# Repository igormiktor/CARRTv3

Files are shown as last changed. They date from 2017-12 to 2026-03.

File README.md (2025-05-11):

# CARRTv3
Cute Autonomous Robot Rover Thing (version 3 -- Raspberry Pi Zero 2 W and Raspberry Pico based)

## Goal 

Goal of this project is to create a small robotic vehicle (CARRT) that can do the following:

- Start in one room of the house;
- Receive a goal position, specified relative to its starting location (e.g., 8 meters North, 4.5 meters West);
- Autonomously make its way to the new position, mapping doors and walls with its Lidar sensor until it finds a path to the goal;
- Build a map as it goes, enabling effective back-tracking whenever it encounters a dead-end.

This is both a hardware and a software project.

The name "CARRT" is thanks to my daughter.

## Version 3: What's New?

[Version 2](https://github.com/igormiktor/CARRTv2) was based on an AVR Mega2560 microcontroller, which proved to have too little memory to maintain a suitably accurate and large enough map of its environment (and it was quite slow at calculating paths).  Version 2 was also unable to track its own position and orientation with sufficient accuracy, making usable map updates effectively impossible.

To overcome these problems, Version 3 uses a Raspberry Pi Zero 2 W as its primary processor, paired with a Raspberry Pico to handle real-time tasks.  The Pi Zero has sufficient RAM to maintain a map of its environment with suitable resolution.  Version 3 also has encoders on its wheels and it uses a BNO055 9-DOF sensor with on-board sensor fusion, so that Euler angles and quaternions can be directly read from it.  The combination of wheel-encoders and direct access to orientation information are estimated to provide suffiently accurate orientation and position information. 

## The Hardware and Software

The hardware consists of a four-wheeled chassis carrying a Raspberry Pi Zero 2 W as its primary processor, paired with a Raspberry Pico to handle real-time tasks.  These are complemented by various other supporting IC subsystems (e.g., a motor driver board, a board with an LCD and keypad, a PWM/Servo-driver board, 3V3<->5V level converters, a battery regulator, etc.)  Navigation is enabled by an BNO055 9-DOF orientation sensor and wheel-encoders.  A Garmin Lidar Lite sensor mounted on a servo allows CARRT to sense obstacles (both furniture and walls) and navigate around them.

The hardware and how it is wired together is described in the [`schematics`](https://github.com/igormiktor/CARRTv3/tree/main/schematics) sub-directory by a [KiCad](https://www.kicad.org/) project file, as well as a PDF of the schematics. Photos of CARRT appear in the [`images`](https://github.com/igormiktor/CARRTv3/tree/main/images) sub-directory.

The software is found in the [`source`](https://github.com/igormiktor/CARRTv3/tree/main/source) directory, with subdirectories for the Pi Zero source code ([`source/rpi`](https://github.com/igormiktor/CARRTv3/tree/main/source/rpi)) and the Pico source code ([`source/pico`](https://github.com/igormiktor/CARRTv3/tree/main/source/pico)).  Code common to both is in [`source/shared`](https://github.com/igormiktor/CARRTv3/tree/main/source/shared).   

The Pi Zero uses I2C to control and monitor the motor driver, the LCD & Keypad, the servo, and the Lidar.  The Pico uses real-time interrupts to track the wheel-encoders and uses a separate I2C to control and monitor the BNO055; the Pico also uses an analog input pin to monitor the level of the LiPo battery that powers the IC circuits.  The Pi Zero and the Pico communicate over a serial link connecting their UARTs.

## Power

CARRTv3 is powered from two sources. A LiPo battery connected to a PowerBoost 1000 module provides 5V power to drive all of the IC-related electronics.  The Pi Zero provides a 3V3 power feed for those subcomponents that need 3V3 power.  A six-pack of AA batteries provides 9V power to the four motors that drive the wheels and to the servo that points the Lidar sensor.

## Specs

* Main processor
    * PI Zero 2 W board
    * Broadcom BCM2710A1, quad-core 64-bit SoC (Arm Cortex-A53 @ 1GHz)
    * 512MB LPDDR2
    * 2.4GHz IEEE 802.11b/g/n wireless LAN, Bluetooth 4.2, BLE, onboard antenna
    * 2 x SPI, 1 x I2C, 1 x UART, no ADC
* Secondary microcontroller
    * Pico RP2040 microcontroller
    * Dual-core Arm Cortex M0+ processor, running up to 133 MHz
    * 264KB of SRAM
    * 2MB of on-board flash memory
    * 2 × SPI, 2 × I2C, 2 × UART, 3 × 12-bit ADC
    * Accurate clock and timer on-chip
    * Temperature sensor
* Power buses
    * First power bus supplied by LiPo battery
        * PowerBoost 1000 generates 5V from the LiPo
        * Pi Zero in turn generates 3V3 power for all devices that need it
        * Both 5V and 3V3 available as required (CARRTv3 is primarily a 3V3 system)
    * Second power bus supplied by a six-pack of AA batteries
        * Provides 9V power to the motors 
        * 4 driving motors (one per wheel)
        * 1 servo motor (points the Lidar across a 180 degree arc) 
* Motor controllers
    * Adafruit Raspberry Pi DC & Stepper Motor Bonnet
    * Uses 4 H-Bridges to power 4 DC motors
    * Each H-Bridge is a TB6612 providing 1.2A per bridge
    * Controlled by the Pi Zero via I2C
* LCD display with keypad
    * 2 x 16 character color LCD
    * 5 button keypad
    * LCD controlled by an HD44780U
    * MCP23017 drives the HD44780U and the keypad
    * MCP23017 connected via I2C to Pi Zero
    * Controlled by Pi Zero via I2C
* PowerBoost 1000
    * Converts LiPo battery to 5V
    * Also serves LiPo batter charger (via USB power connection)
    * Provides "power off" control via grounding of an "enable" pin 
    * Battery level pin read by analog Pico pin (level shifted by resistor bridge to 3V3)
* BNO055 9-DOF Orientation Sensor
    * 3 sensors in one device
        * Triaxial 16bit gyroscope
        * Triaxial 14bit accelerometer
        * Geomagnetic sensor
    * 32-bit Cortex M0+ microcontroller runs sensor fusion software,
    * Outputs Euler angles, quaternions, rotation vector, linear acceleration, gravity, heading 
    * Controlled by Pico via I2C
* PCA9685 16-channel PWM/Servo driver
    * 16 independent PWM channels
    * Used to control the servo
    * Controlled by Pi Zero via I2C
    * Servo powered by 9V bus
* TXB0104 Bi-Directional Level Shifter
    * Performs bidirectional level shifting between 5V and 3V3 
    * Auto-detects the direction
    * Not suitable for I2C level-shifting
* BSS138 Bi-Directional Logic Level Shifter
    * 4-channel I2C-safe bidirectional logic level converter 
    * 4 BSS138 FETs with 10K pullups
    * Logic-shift only, no loads possible on high side
* Wheel-encoders 
    * On two front wheels
    * Encoders are 5V subsystems
    * Read by Pico after level-shifting by TXB0104
* Hiwonder HPS-2018MG servo
    * Working voltage 6.8 - 10.4V
    * Rotation range 0 - 180 degress 
    * Servo accuracy 0.3 degrees
    * Pulse period 20ms
    * Duty cycle 0.5ms - 2.5ms
    * Controlled by Pi Zero via I2C via PCA9685
* Garmin Lidar Lite v3
    * Mounted on the HPS-2018MG servo
    * Resolution 1cm
    * Accuracy +/- 2.5cm
    * Range 5cm to 40m
    * Laser wavelength 905nm
    * Lidar is a 5V subsystem
    * Controlled by PI Zero via I2C (level-shifted by BSS138)
* PS1240 piezoelectric buzzer
    * For success beeps and error tones

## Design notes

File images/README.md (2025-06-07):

# The evolution of CARRTv3 

A series of photos capturing the evolution of CARRTv3 from the very beginning of prototyping.

## Prototyping

A very early prototype combined a Raspberry Pi Zero with an Adafruit Pro Trinket (3V3) for realtime tasks. It was powered by 12V from a pack of 8 x AA cells.  This 12V feed powered both all motors and also feed a UBEC to generate 5.2V output to power the ICs.  The prototype also included an LCD with keypad. a 9DOF BNO055 sensor, and a motor-driver board.  The two photos below show the configuration without (left) and with (right) the drive motors connected.  For prototypoing, the various boards and components are velcroed onto a transparent plastic board.

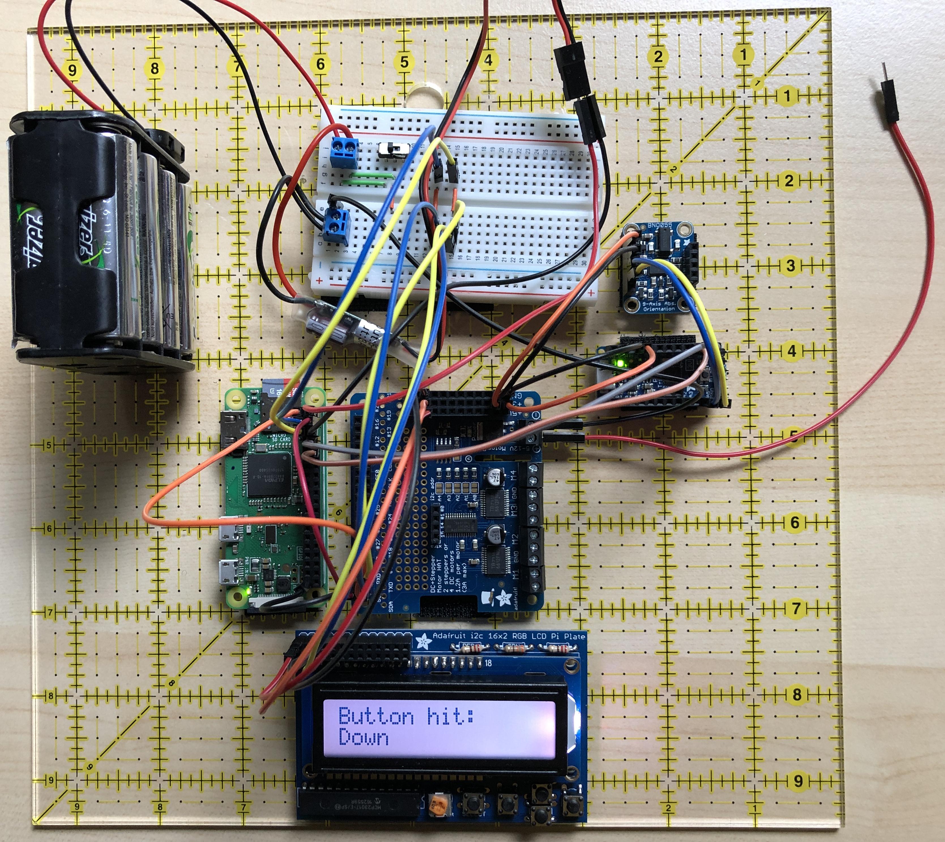
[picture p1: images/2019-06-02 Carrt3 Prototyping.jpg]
Early prototype: RPi Zero, Adafruit Trinket, 9DOF sensor, LCD + keypad, motor board
[]("https://github.com/igormiktor/CARRTv3/blob/main/images/2019-06-02%20Carrt3%20Prototyping.jpg")
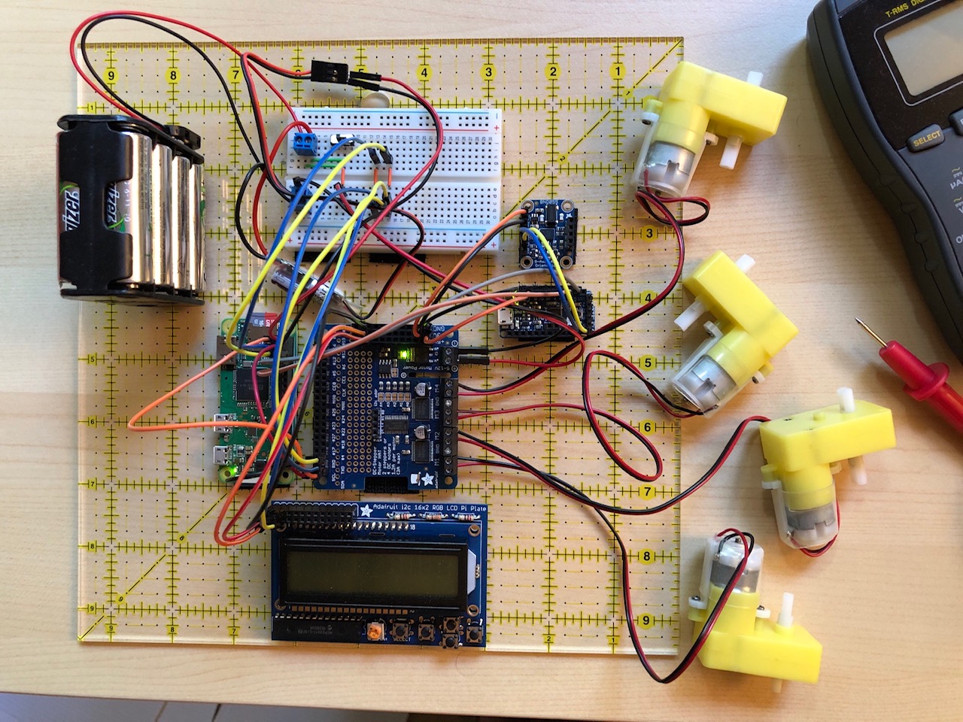
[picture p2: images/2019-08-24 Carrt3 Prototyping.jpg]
Early prototype: RPi Zero, Adafruit Trinket, 9DOF sensor, LCD + keypad, motor board, and motors
[]("https://github.com/igormiktor/CARRTv3/blob/main/images/2019-08-24%20Carrt3%20Prototyping.jpg)

The power source was not sufficently stable to reliably power the RPi Zero (and other ICs).  The boards themselves also took up too much space (cm<sup>2</sup>) to all fit when mounted on the vehicle chassis.  So while useful for initial testing and exploration, the configuration was updated as follows:

* An AdaFruit PowerBoost 1000C, powered by a 3.7v 2,500mAh LiPo battery replaces the 8 x AA cells and UPEC combination to power the RPi Zero (and other ICs).
    * A set of 6 x AA batteries (producing 9V) is retained on a separate power bus to power motors of various kinds.
* An RPi Pico replaces the Adafruit Pro Trinket (3V3).  The Pico provides a much more capable microcontroller, having 2 cores, more memory, and running at 10x the clock speed of the Trinket (133MHz vs 12MHz).
* A much smaller motor board replaces the original motor board.  The original was an RPi "shield" (same footprint as a fullsize RPi). The new one is a much smaller RPI "bonnet", with the much smaller footprint of an RPI Zero.
* A PCA9685 PWM board provides 16 x 12 bit PWM outputs to drive servo motors.

## Organizing Electronics

To facilitate attachment of printed circuit boards (PCBs) and the wiring between these, I created a 3D-printed plastic "riser".  The various PCBs are attached to the riser, allowing wiring to be run under or over the riser, keeping the wiring a bit neater.  The riser (with attached PCBs) is then attached to the chassis.

Not all the PCBs could fit on the riser.  As a result the motor driver PCB (an Adafruit "bonnet") is actually attached underneath the top plate of the chassis (in the area below the breadboards).  A 3D-printed holder for the LiPo battery is also attached underneath the top plate (located roughly under the PowerBoost and the RPi Zero).

Finally, a small breadboard is also installed on the lower plate of the chassis to distribute 9V power to all motors.  That small breadboard also carries an on-off switch for the 9V power circuit and an indicator LED that lights when 9V power is on.  The 9V battery pack (6 x AA) simply sits in the well between the four drive motors.

The following images show (L-to-R):
* The plastic riser with PCBs attached (but not wired).
* The plastic riser adjacent to the assembled chassis.
* The dissassembled (partially wired) chassis showing (L-to-R)
    * The bottom plate, with 4 motors and 9V breadboard.
    * The top plate (inverted), showing the motor driver PCB, and the LiPo battery holder.
    * The riser with PCBs (partially wired for testing).

[Riser Deck, with electronics]("https://github.com/igormiktor/CARRTv3/blob/main/images/2024-05-25%20Electronics%20Deck.jpg")
[Riser deck adjacent to the assembled chassis]("https://github.com/igormiktor/CARRTv3/blob/main/images/2024-05-25%20Chassis%2BElectronics%20Deck.jpg")
[Dissassembled (partially wired) chassis]("https://github.com/igormiktor/CARRTv3/blob/main/images/2024-05-26%20L-to-R%20Chassis%20bottom%2C%20underneath%20Chassis%20top%2C%20Electronics%20deck.jpg")

This layer-cake assembly (and especially the riser carrying the PCBs witht he primary electronics) simplifies assembly and disassembly, and facilitated "test as you assemble.  The following images show how it all comes together (L-to-R):
* The electronics-carrying riser mounted on top of the vehicle chassis.
* The battery-holder mounted under the chassis top plate.
* The battery-holder and motor driver PCB mounted under the chassis top plate.

[Electronics-carrying riser mounted on top of the vehicle chassis]("https://github.com/igormiktor/CARRTv3/blob/main/images/2024-05-25%20Chassis%20with%20Electronics%20Deck.jpg")
[Riser Deck, with electronics]("https://github.com/igormiktor/CARRTv3/blob/main/images/2024-05-25%20Battery%20under%20Chassis%20top.jpg")
[Riser Deck, with electronics]("https://github.com/igormiktor/CARRTv3/blob/main/images/2024-05-25%20Chassis%20%2B%20battery%20holder%20(L)%20%2B%20motor%20driver%20(R).jpg")

## Wiring and Power-up

Wiring and power-up testing started early and continued throughout assembly.  This is depicted in the following images (L-to-R):
* A minimal assembly and wiring under power (electronics on riser only)
* All layers powered, LCD and drive motors running

[Minimal assembly and wiring under power]("https://github.com/igormiktor/CARRTv3/blob/main/images/2024-05-26%20Minimal%20Assembly%20Powered.jpg")
[All layers powered, LCD and drive motors running]("https://github.com/igormiktor/CARRTv3/blob/main/images/2024-06-03%20Motors%20running%20under%20electronic%20control.jpg")

Final wiring was accomplished with hook-up wire (instead of breadboarding wire).  As a general rule, longer wire reaches run under the riser; shorter ones run over the riser and PCBs.  The color code for the hook-up wires is:
| Color  | Purpose |
| :---:  | :--- |
| Black  | Ground |
| Red | Power (5V) |
| Orange | Power (3V3) |
| Blue | I2C SDA (data) |
| Yellow | I2C SCL (clock) |
| Grey | Serial TX-RX |
| Dark Blue | Serial RX-TX |
| Green | PWM and GPIO (various) |
| White | GPIO (various) |

Images below show a nearly fully wired CARRTv3. The only wires missing are those connecting the motor driver PCB and those connecting the Garmin Lidar (which is not yet installed).  These images show views from the front and rear; from the left and right sides; and final a top view.

[Front view]("https://github.com/igormiktor/CARRTv3/blob/main/images/2025-04-08%20CARRTv3%20Front%20View.jpg")
[Rear view]("https://github.com/igormiktor/CARRTv3/blob/main/images/2025-04-08%20CARRTv3%20Rear%20View.jpg")

[Left view]("https://github.com/igormiktor/CARRTv3/blob/main/images/2025-04-08%20CARRTv3%20Left%20View.jpg")
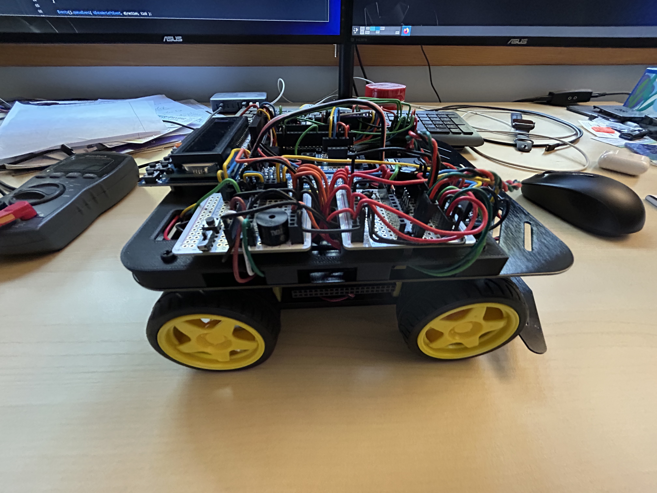
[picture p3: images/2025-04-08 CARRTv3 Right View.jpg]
Right view
[]("https://github.com/igormiktor/CARRTv3/blob/main/images/2025-04-08%20CARRTv3%20Right%20View.jpg")

[Top view]("https://github.com/igormiktor/CARRTv3/blob/main/images/2025-04-08%20CARRTv3%20Top%20View.jpg")

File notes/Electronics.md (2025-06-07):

# Electronics

## Wiring

| Color  | Purpose |
| :---:  | :--- |
| Black  | Ground |
| Red | Power (5 V) |
| Orange | Power (3.3 V) |
| Blue | I2C SDA |
| Yellow | I2C SCL |
| Grey | UART TX-RX |
| Dark Blue | UART RX-TX |
| Green | PWM and GPIO (various) |
| White | GPIO (various) |

## Power Voltages

| Point of Measurement | Voltage |
| :--- | :---: |
| Power Boost 1000C Output (at posts) | 5.19 V |
| RPI Zero Output (at RPi Zero) | 5.14 V |
| On 5V Power Rail | 5.08 V |
| On 3.3V Power Rail | 3.25 V |
| Input to Pico (before diode) | 5.08 V |
| Input to Pico (after diode) | 4.3 V |
| RPI Pico Output (3V) | 3.3 V |
| Motor Batteries Output (at posts) | 10.4 V (8 batteries) |
| Motor Hat (at input) | 10.4 V (8 batteries) |
| Motor Batteries Output (at posts) | 7.8 V (6 batteries) |
| Motor Hat (at input) | 7.8 V (6 batteries) |

## Drive Motor Operations

| Operation | Current |
| :--- | :---: |
| Idle | 0.0007 A |
| Single motor start  | 0.3 - 0.6 A |
| Single motor run | 0.2 - 0.3 A |
| All motor start | 1.2 - 2.5 A |
| All motor run | 0.8 - 0.9 A |

* Switch directly by manual switch on lower (12V) distribution panel

## Raspberry Pi Zero 2 W Operations

| Operation | Current |
| :--- | :---: |
| Idle | 100 mA |
| Start up | 200 mA |
| Computing | 350 mA |

* Switched directly by PowerBoost 1000C using a manual switch (on the upper-rear distribution panel) that grounds the Enable Pin on the PowerBoost.

## Raspberry Pico Operations

| Operation | Current |
| :--- | :---: |
| Idle | 18 mA |
| Start up | 15 mA |
| Max possible  | 200 mA |

* Required switching transistor:  2N2222
* Required transistor base resistor:  2.2 KOhms
* Installed on upper=rear distribution panel
* Automatically switched by RPi Zero via GPIO17 on Pin 11

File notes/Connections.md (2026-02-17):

# Wiring Connections

## Rapsberry Zero

| To | Function | Pin | | Pin | Function | To |
| :---: |  :---: | :---: | :---: | :---: | :---:  | :---: |
| Other 3V3 ICs | 3V3 |  1 |  |  2 | 5V (in) | PowerBoost 5V out |
| I2C Bus RPi0 | I2C SDA |  3 |  |  4 | |  |
| I2C Bus RPi0 | I2C SCL |  5 |  |  6 | | |
| | |  7 |  |  8 | UART TX | Pico UART RX |
| | |  9 |  | 10 | UART RX | Pico UART TX |
| Pico On/Off 2N2222 base  | GPIO17  | 11 |  | 12 |  |  |
| | | 13 |  | 14 | GND | TXB0104 GND |
| | | 15 |  | 16 | GPIO23 | Monitor PowerBoost LPO for battery low |
|  TXB0104 OE Pin | 3V3 | 17 |  | 18 |  |  |
| | | 19 |  | 20 |  |  |
| | | 21 |  | 22 |  |  |
| | | 23 |  | 24 |  |  |
| | | 25 |  | 26 |  |  |
| | | 27 |  | 28 |  |  |
| | | 29 |  | 30 |  |  |
| | | 31 |  | 32 | PWM0 | Buzzer |
| | | 33 |  | 34 | GND | Common Gnd |
| | | 35 |  | 36 | GPIO16 | Shutdown Button |
| | | 37 |  | 38 |  |  |
| | | 39 |  | 40 |  |  |

## Rapsberry Pico

| To | Function | Pin | | Pin | Function | To |
| :---: |  :---: | :---: | :---: | :---: | :---: | :---: |
| Debug RX (Black/Yellow) | UART0 TX |  1 |  | 40 | VBUS | |
| Debug TX (White/Orange) | UART0 RX |  2 |  | 39 | VSYS | 5V Motor Board via 1N4001 diode |
| Debug Gnd (Red/Black) | Gnd |  3 |  | 38 | Gnd | BNO055  |
| | |  4 |  | 37 | | |
| | |  5 |  | 36 | 3V3 | BNO055 |
| RPi0 UART RX | UART1 TX |  6 |  | 35 | | |
| RPi0 UART TX | UART1 RX |  7 |  | 34 | | |
| | |  8 |  | 33 |  |  |
| | |  9 |  | 32 | ADC1 | (GPIO27) ADC to PowerBoost Batt Pin (via V-Divider) |
| | | 10 |  | 31 | ADC0 | (GPIO26) ADC to 9V Batt+ (via V-Divider) |
| I2C Bus Pico | I2C0 SDA | 11 |  | 30 |  |  |
| I2C Bus Pico | I2C0 SCL | 12 |  | 29 |  |  |
| | | 13 |  | 28 |  |  |
| | | 14 |  | 27 |  |  |
| | | 15 |  | 26 |  |  |
| | | 16 |  | 25 |  |  |
| | | 17 |  | 24 |  |  |
| | | 18 |  | 23 | Gnd | Gnd via 2N2222 controlled by Zero GPIO17 |
| Left Encoder | GPIO14 | 19 |  | 22 |  |  |
| Right Encoder | GPIO15 | 20 |  | 21 |  |  |

### Rapsberry Pico SWD (Debug) Pins
(In order from Pin 20 side to Pin 21 side)
| To | Function | Pin |
| :---: |  :---: | :---: |
| Debug CLK (Orange) | SWCLK |  SWD1 | 
| Debug Gnd (Black)  | GND |  SWD2 | 
| Debug IO (Yellow)  | SWIO  |  SWD3 |  

## Adafruit PowerBoost 1000C

| Pin | Function | To |
| :---: | :---: | :---: |
| USB | USB 5V (charge in) |  |
| Bat | Battery Input (3.0-4.2V) | Pico pin 32 (ADC1) via V-Divider |
| Vs | Max(USB, LiPo) |  |
| EN | Enable (Ground to disable) | On/Off Switch |
| GND | Gound |  |
| LBO | Low Battery Signal (toggles from Bat to 0V) | (not 3.3V safe!) RPi0 pin 16 (GPIO23) via TXB0104 |
| GND | Ground | Common Gnd |
| 5Vo | Output 5V (5.2-5.0 V) | Common IC 5V rail  |
|

## BNO055

| Pin | Function | To |
| :---: | :---: | :---: |
| Vin | Power in (3.3-5.0V) | Pico 3V3 |
| 3vo | 3.3V output |  |
| GND | Ground | Pico Gnd |
| SDA | I2C data | Pico I2C0 SDA |
| SCL | I2C clock | Pico I2C0 SCL |
| RST | HW reset (set low, then high) |  |
| PS0 | Mode change pin 0 |  |
| PS1 | Mode change pin 1 |  |
| INT | HW interrupt (goes high 3V) |  |
| ADR | I2C address (default = 0x29; high = 0x28) |  |

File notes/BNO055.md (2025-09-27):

https://learn.adafruit.com/bno055-absolute-orientation-sensor-with-raspberry-pi-and-beaglebone-black/webgl-example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

https://aiinsemi.com/post/Why%20Your%20BNO055%20Sensor%20is%20Giving%20Incorrect%20Data_%20Common%20Calibration%20Issues.html

https://forums.adafruit.com/viewtopic.php?f=25&t=108290&p=541754#p541754

by gammaburst » 16 Dec 2016 22:53
"sensor holds its default configuration P1" -- Do you mean that writing AXIS_REMAP_CONFIG and AXIS_REMAP_SIGN had no effect? Perhaps you are writing them at the wrong time - the Bosch documentation is sometimes vague and insufficient.

Here's my BNO055 startup procedure:
- assert RST
- wait one microsecond
- deassert RST
- wait 800 milliseconds
- (optional) write the two axis remap registers
- (optional) write my previously stored calibration profile into registers 0x55-0x6A
- write 0x0C (NDOF mode) into OPR_MODE register
- wait 10 milliseconds
- begin reading sensor and fusion data registers every 10 milliseconds.

Beware the BNO055 datasheet uses two spellings:
- AXIS_MAP_CONFIG and AXIS_MAP_SIGN
- AXIS_REMAP_CONFIG and AXIS_REMAP_SIGN.

Be sure you have the current BNO055 datasheet version 1.4.

Axises can be remaped only in OPERATION_MODE_CONFIG state.
Reading and writing calibration data is only possible in this state.

How are you testing your quaternion-to-euler conversion? Numbers via the serial port? 3D graphics display? Beware the bunny/Processing example is broken.

Remember to normalize the quaternion.

If you use other people's vector and quaternion equations, beware of different axes conventions. This gets confusing!

During my experiments with Adafruit's BNO055 library I used this code to convert quaternion to Euler. It's one of the fixes that I applied to the bunny/Processing example:

/* Convert quaternion to Euler, because BNO055 Euler data is broken */
  imu::Quaternion q = bno.getQuat();
  q.normalize();
  float temp = q.x();  q.x() = -q.y();  q.y() = temp;
  q.z() = -q.z();
  imu::Vector<3> euler = q.toEuler();
  Serial.print(F("Orientation: "));
  Serial.print(-180/M_PI * euler.x());  // heading, nose-right is positive, z-axis points up
  Serial.print(F(" "));
  Serial.print(-180/M_PI * euler.y());  // roll, rightwing-up is positive, y-axis points forward
  Serial.print(F(" "));
  Serial.print(-180/M_PI * euler.z());  // pitch, nose-down is positive, x-axis points right
  Serial.println(F(""));

I have also successfully used Wikipedia's info and equations:
https://en.wikipedia.org/wiki/Conversio ... Conversion

https://en.wikipedia.org/wiki/Conversion_between_quaternions_and_Euler_angles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

https://forum.arduino.cc/t/convert-adafruit-bno055-quaternion-angles-to-euler-angles/399436/5

float yaw   = atan2(2.0f * (q[1] * q[2] + q[0] * q[3]), q[0] * q[0] + q[1] * q[1] - q[2] * q[2] - q[3] * q[3]);
float pitch = -asin(2.0f * (q[1] * q[3] - q[0] * q[2]));
float roll = atan2(2.0f * (q[0] * q[1] + q[2] * q[3]), q[0] * q[0] - q[1] * q[1] - q[2] * q[2] + q[3] * q[3]);[/quote]

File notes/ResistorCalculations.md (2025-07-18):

# Resistor Calculations

## Motor Battery Level Monitoring

Need to monitor motor battery voltage (nominally 6 x 1.5V = 9V).  
We need to create a resistor divider to ensure the output is not over 3.3V.

### Range of motor battery voltages (6 x AA batteries)
| Type | Full charge | Functionally Dead |
| :---: |  :---: | :---: |
| Akaline | 9.9V | 7.5V |
| NiMH | 8.7V | 7.2V |
| Lithium | 10.8V | 7.8V |

* Input Full V = 8.7 - 10.8 V
* Input Dead V = 7.2 - 7.8 V
* R1 = 180K Ohm
* Output Full V = 2.72 - 3.38 V --> Pico Pin GPIO27
* Output Dead V = 2.35 - 2.44 V --> Pico Pin GPIO27
* R2 = 82K Ohm
* Ground 
* Current through bridge ~0.05 mA  

### Range of measured voltages (at Pico Pin GPIO27)

| Type | Full charge | Functionally Dead |
| :---: |  :---: | :---: |
! Akaline | 3.10V       | 2.35V |
| NiMH    | 2.72V       | 2.25V |
| Lithium | 3.38V       | 2.44V |

## PowerBoost 1000C LBO (Low Battery) Monitoring

LBO drops to 0V when PowerBoost detects battery low voltage (<3.2V).  
However, LBO is pulled up to Vin (up to 5.25V), 
so we need to create a resistor divider to ensure the output 
is always under 3.3V.

* Input V = 5.25 V   <-- PowerBoost LBO Pin
* R1 = 39K Ohm
* Output V = 3.3 V and 0.05 mA  --> Pico Pin GPIO26
* R2 = 68K Ohm
* Ground   

## Encoders

Encoders on the wheels are 5V devices, need to convert them to 3.3V.  
We use the TXB0104 to the the 5V -> 3V3 conversion.

We need two of these conversions (one pair of TXB0104 pins per encoder).

Encoder Pins:

* Pin 1 --> Signal pin (Green)
* Pin 2 <-- +5V power pin (Red)
* Pin 3 --> Gnd (Black)

## Pico power control (on/off from RPi Zero)

Use a 2N2222 transistor on the ground for the Pico to allow the RPi0 to turn it 
on and off

* 2N2222 collector <-- Pico GND
* 2N2222 base <-- 10 KOhm resistor <-- RPi0 GPIO17 (pin 11)
* 2N2222 emitter --> system GND 

Setting RPi0 GPIO17 (pin 11) LOW turns off the Pico; setting RPi0 GPIO17 HIGH turns on the Pico.

## Sources

Resistor calculator: [http://howardtechnical.com/voltage-divider-calculator/](http://howardtechnical.com/voltage-divider-calculator/)

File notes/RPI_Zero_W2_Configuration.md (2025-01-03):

# Raspberry Pi Zero 2 W Configuration

## Goal

Goal is to minize the amperage that the RPi Zero 2 W draws.  Power comes from a LiPo battery through an Adafruit
Powerboost 1000C that has a 2A internal switch (~2.5A peak limiting). The RPi Zero then powers the RP2040 (5V feed) and 
all the secondary chips (3.3V feed).  Motors are powered by a separate power circuit.

## Power Demands

The main power consumers are:

| Device | Recommended Power <br /> Supply Capacity | Typical Bare-Board <br /> Current Draw | Max Board <br /> Current Draw | 
|:---:|:---:|:---:|:---:|
| Raspberry Pi Zero W | 1.2 A | 150 mA | ~0.8 A |
| Raspberry Pi Zero 2 W | 2.0 A | 350 mA | ~1.3 A |
| Raspberry Pico | 0.5 A | 35 mA  | ~100 mA | 

## Minimizing Power Demand

To minimize the RPi Zero power consumption, we make the following configuration changes.

### Turn off blue tooth
To turn off blue tooth (which also makes the best UART available for serial communications) **_add_** the following 
line to `/boot/config.txt` under section `[all]`:

```bash
dtoverlay=disable-bt
```

### Turn off HMDI.
To turn off HMDI first **_comment out_** the following line in `/boot/config.txt`:

```bash
dtoverlay=vc4-kms-v3d
```
and then **_add_** the following line to `/etc/rc.local`:

```bash
/usr/bin/tvservice -o
```

## Provide a Linux shutdown button

To provide a button to trigger a controlled Linux shutdown, I configured GPIO 16 to trigger a controlled
shutdown by adding the following line to `/boot/config.txt` under section `[all]`: 

```bash
dtoverlay=gpio-shutdown,gpio_pin=16,active_low=1,gpio_pull=up
```

And then make sure that in file `/etc/systemd/logind.conf` the line for HandlePowerKey appears as follows:

```bash
HandlePowerKey=poweroff
```

If it is not, the best solution is to create the directory `/etc/systemd/logind.conf.d` and then in that directory
create a file (such as `handlePowerKey.conf` or `poweroff.conf`) containing:

```bash
[Login]
HandlePowerKey=poweroff
```

Note that the default GPIO for poweroff (GPIO 3) is needed for I2C, so it can't be used for the shutdown function.

## Set pigpiod to run

```bash
systemctl enable pigpiod
systemctl start pigpiod
```

## Install wiringpi (especially for the gpio command)

Clone https://github.com/WiringPi/WiringPi and follow the instructions to build and install.

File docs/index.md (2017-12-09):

---
layout: home
#title: CARRT &mdash; an Autonomous Path-Finding Rover
#permalink: /
---

# CARRT v3

Goal of this project is to create a small robotic vehicle (CARRT) that can do the following:

- Start in one room of a house;
- Receive a goal position relative to its current position;
- Autonomously make its way to the goal position, mapping doors and walls with its lidar until it finds a path to the goal;
- Build a map as it goes, enabling effective back-tracking whenever it hits a dead-end.

Version 3 of CARRT is based on a Raspberry Zero W.

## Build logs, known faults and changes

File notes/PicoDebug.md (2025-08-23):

# Connecting RPi Debug Probe to Pico

## Debugger Connections (Debug Port)

Use the orange-black-yellow connector
* Orange wire goes to Pico SWCLK (left Debug pin)
* Black wire goes to Pico GND (middle Debug pin) 
* Yellow wire goes to Pico SWDIO (right Debug pin)

## Serial Connections (UART Port)

Using the white-red-black connector
* White wire goes to Pico Pin 2, GP1
* Red wire goes to Pico Pin 3, GND
* Black wire goes to Pico Pin 1, GP0

Using the orange-black-yellow connector
* Orange wire goes to Pico Pin 2, GP1
* Black wire goes to Pico Pin 3, GND
* Yellow wire goes to Pico Pin 1, GP0

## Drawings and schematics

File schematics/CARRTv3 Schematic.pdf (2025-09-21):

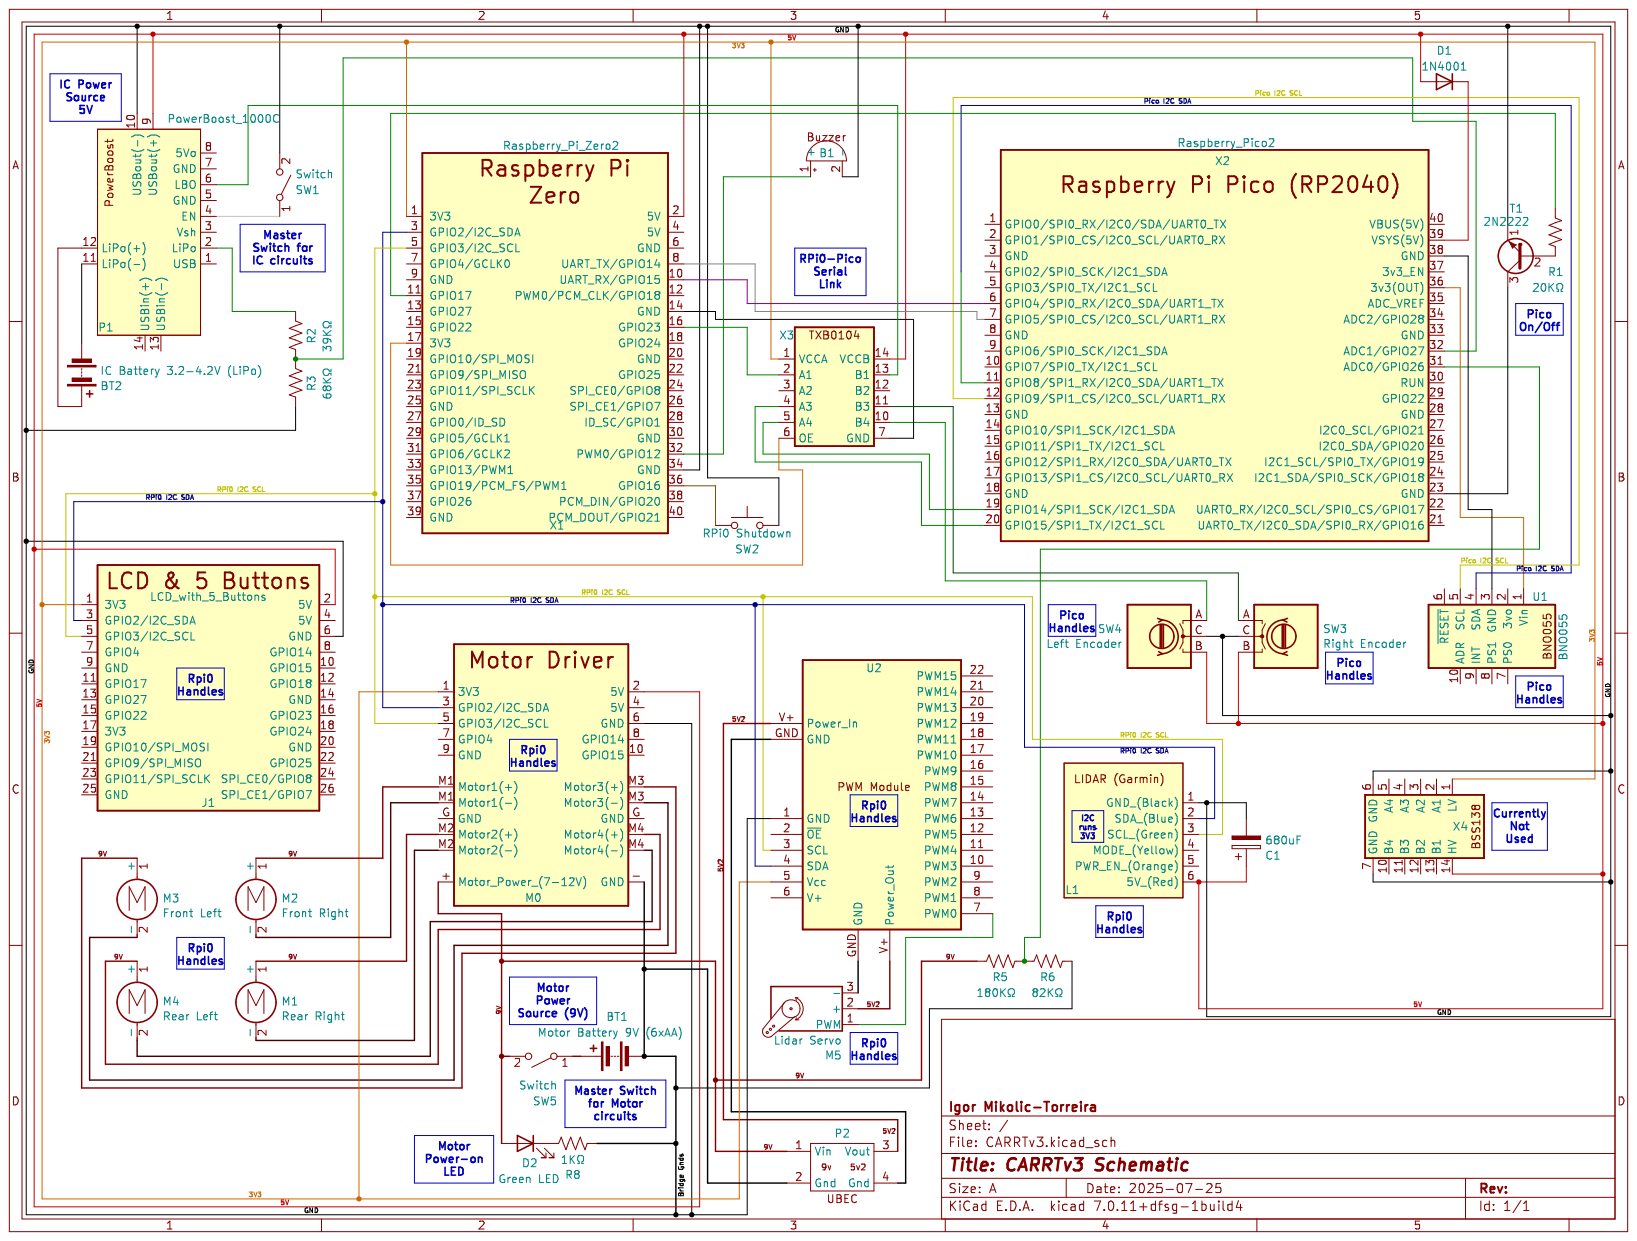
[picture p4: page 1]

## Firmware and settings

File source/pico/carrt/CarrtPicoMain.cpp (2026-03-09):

/*
    CarrtPicoMain.cpp - CARRT-Pico's main function.
    Initializes and hands off to the Main Process.

    Copyright (c) 2026 Igor Mikolic-Torreira.  All right reserved.

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
    You should have received a copy of the GNU General Public License
    along with this program.  If not, see <http://www.gnu.org/licenses/>.
*/

#include "BNO055.h"
#include "Batteries.h"
#include "BuildInfo.h"
#include "CarrtError.h"
#include "CarrtPicoDefines.h"
#include "CarrtPicoReset.h"
#include "Clock.h"
#include "Core1.h"
#include "CoreAtomic.hpp"
#include "DebugUtils.hpp"
#include "Encoders.h"
#include "EventHandlers.h"
#include "EventManager.h"
#include "EventProcessor.h"
#include "HeartBeatLed.h"
#include "I2C.h"
#include "MainProcess.h"
#include "OutputUtils.hpp"
#include "PicoState.h"
#include "SerialLinkPico.h"
#include "SerialMessageProcessor.h"
#include "SerialMessages.h"

#if 0    // Used to test compile definitions inherit properly in cmake build

    #if defined( DEBUGUTILS_ON ) && DEBUGUTILS_ON
        #pragma message "DEBUGUTILS_ON = ON"
    #elif defined( DEBUGUTILS_ON )
        #pragma message "DEBUGUTILS_N = OFF"
    #else
        #pragma message "DEBUGUTILS_N = undef"
    #endif

    #if defined( USE_CARRTPICO_STDIO ) && USE_CARRTPICO_STDIO
        #pragma message "USE_CARRTPICO_STDIO = ON"
    #elif defined( USE_CARRTPICO_STDIO )
        #pragma message "USE_CARRTPICO_STDIO = OFF"
    #else
        #pragma message "USE_CARRTPICO_STDIO = undef"
    #endif

    #if defined( DEBUGCARRTPICO ) && DEBUGCARRTPICO
        #pragma message "DEBUGCARRTPICO = ON"
    #elif defined( DEBUGCARRTPICO )
        #pragma message "DEBUGCARRTPICO = OFF"
    #else
        #pragma message "DEBUGCARRTPICO = undef"
    #endif

    #if defined( BUILDING_FOR_PICO ) && BUILDING_FOR_PICO
        #pragma message "BUILDING_FOR_PICO = ON"
    #elif defined( BUILDING_FOR_PICO )
        #pragma message "BUILDING_FOR_PICO = OFF"
    #else
        #pragma message "BUILDING_FOR_PICO = undef"
    #endif

#endif    // Checking compile definitions

namespace
{
    void initializeNoFailHardware();
    void initializeFailableHardware();
    void setupMessageProcessor( SerialMessageProcessor& smp );
    void setupEventProcessor( EventProcessor& ep );
    void sendReady( SerialLinkPico& link );
}    // namespace

constexpr int kSerialMessageHandlerReserveSize = 24;
constexpr int kEventHandlerReserveSize = 20;

////////////////////////////////////////////////////////////////////////////////

int main()
{
    CoreAtomic::CAtomicInitializer theInitializationIsDone;
    PicoState::initialize();

    initializeNoFailHardware();

    // Open the serial link to RPi0
    SerialLinkPico rpi0;

    try
    {
        initializeFailableHardware();

        output2cout( "CARRT Pico started, hardware initialized, both cores running." );
        output2cout( "CARRT Pico version", CarrtPicoVersion::versionStr(), "with features",
                     CarrtPicoVersion::features() );
        output2cout( "CARRT Pico build date", CarrtPicoVersion::buildDate(),
                     CarrtPicoVersion::buildTime() );
        output2cout( "CARRT Pico Git Hash", CarrtPicoVersion::hashFull() );
        output2cout( "CARRT Pico Git Hash (short)", CarrtPicoVersion::hashShort() );
        if ( CarrtPicoVersion::buildIsDirty() )
        {
            output2cout( "WARNING: CARRT Pico build is DIRTY" );
        }

        // Set up message processor
        SerialMessageProcessor smp( kSerialMessageHandlerReserveSize, rpi0 );
        setupMessageProcessor( smp );

        // Set up event processor
        EventProcessor ep( kEventHandlerReserveSize );
        setupEventProcessor( ep );

        // Report we are started and ready to receive messages
        sendReady( rpi0 );

        // Default starting values
        // (at least for now while testing, RPi0 can change these via msg)
        // TODO: Perhaps eventual make this allMsgsSendOff()
        PicoState::allMsgsSendOn();

        MainProcess::runMainEventLoop( Events(), ep, smp, rpi0 );
    }

    catch ( const CarrtError& e )
    {
        // Expected errors, report the error...
        ErrorReportMsg err( kPicoFatalError, e.errorCode(), Clock::millis() );
        err.sendOut( rpi0 );

        output2cout( "Fatal error", e.errorCode(), e.what() );
    }

    catch ( const std::exception& e )
    {
        // Known but unexpected error, report these...
        int errCode{ makePicoErrorId( kPicoMainError, 1, 0 ) };
        ErrorReportMsg err( kPicoFatalError, errCode, Clock::millis() );
        err.sendOut( rpi0 );

        output2cout( "Fatal error of unexpected nature", e.what() );
    }

    catch ( ... )
    {
        // Unknown errors, report these
        int errCode{ makePicoErrorId( kPicoMainError, 2, 0 ) };
        ErrorReportMsg err( kPicoFatalError, errCode, Clock::millis() );
        err.sendOut( rpi0 );

        output2cout( "Fatal error of unknown type" );
    }

    // From this point, recovering from serious error we can't handle
    // No matter what, this proceess ends in resetting Pico

    output2cout( "Pico frozen and displaying fast LED strobe" );

    // Just spin and put HeartBeatLed on fast strobe
    constexpr int kWaitTimeInMin{ 1 };
    for ( int i{ 0 }; i < kWaitTimeInMin * 60 * 10; ++i )
    {
        Clock::sleep( 100ms );
        HeartBeatLed::toggle();

        // See if we get a sent a reset message
        if ( rpi0.isReadable() )
        {
            auto msgType = rpi0.getMsgType();
            if ( msgType && *msgType == MsgId::kResetPicoMsg )
            {
                PicoReset::reset( rpi0 );
            }
        }

        // If no reset msg, we keep strobing the LED
    }

    // If we get here, just force reset
    output2cout( "Fatal reset" );
    PicoReset::fatalReset();

    return 0;
}

////////////////////////////////////////////////////////////////////////////////

namespace
{

    void initializeNoFailHardware()
    {
        // Nothing in this function throws or even fails

#if USE_CARRTPICO_STDIO
        // Initialize C/C++ stdio (used for status output and debugging)
        stdio_init_all();
#endif

        // Initialize state
        PicoState::initialize();

        // Set up Pico's I2C (to talk with BNO055)
        I2C::initI2C();

        // Initialize the heartbeat LED
        HeartBeatLed::initialize();

        // The encoders are set up on Core1

        // Initialize ADC for batteries
        Batteries::initBatteries();
    }

    void initializeFailableHardware()
    {
        // These function calls may throw

        // Launch Core1
        Core1::launchCore1();

        // If we get here, guaranteed Core1 is running and in its
        // main event loop.  So perfect time to queue this future
        // event to trigger initialization of BNO055.
        // Note future b/c BNO055 needs nearly 1 sec to be ready to accept I2C.
        Core1::queueEventForCore1( EvtId::kBNO055InitializeEvent, BNO055::kWaitAfterPowerOnReset );

        // Tell Core1 to initialize the encoders
        // Core1 does it so the interrupts go to Core1
        Core1::queueEventForCore1( EvtId::kInitEncoders );
    }

    // Debug/test might not call (e.g., use smp in DumpByte mode)
    [[maybe_unused]] void setupMessageProcessor( SerialMessageProcessor& smp )
    {
        // Only register those messages we actually can receive
        // Messages that are only outgoing don't need to be registered
        smp.registerMessage<PingMsg>( MsgId::kPingMsg );
        smp.registerMessage<PingReplyMsg>( MsgId::kPingReplyMsg );
        smp.registerMessage<VersionRequestMsg>( MsgId::kVersionRequestMsg );
        // smp.registerMessage<VersionMsg>( MsgId::kVersionMsg );
        // smp.registerMessage<PicoReadyMsg>( MsgId::kPicoReady );
        // smp.registerMessage<PicoNavStatusUpdateMsg>( MsgId::kPicoNavStatusUpdate );
        // smp.registerMessage<PicoSaysStopMsg>( MsgId::kPicoSaysStop );
        smp.registerMessage<MsgControlMsg>( MsgId::kMsgControlMsg );
        smp.registerMessage<ResetPicoMsg>( MsgId::kResetPicoMsg );
        // smp.registerMessage<TimerEventMsg>( MsgId::kTimerEventMsg );
        smp.registerMessage<TimerControlMsg>( MsgId::kTimerControl );
        smp.registerMessage<BeginCalibrationMsg>( MsgId::kBeginCalibration );
        smp.registerMessage<RequestCalibrationStatusMsg>( MsgId::kRequestCalibStatus );
        // smp.registerMessage<CalibrationInfoUpdateMsg>( MsgId::kCalibrationInfoUpdate );
        smp.registerMessage<SetAutoCalibrateMsg>( MsgId::kSetAutoCalibrate );
        smp.registerMessage<ResetBNO055Msg>( MsgId::kResetBNO055 );
        // smp.registerMessage<NavUpdateMsg>( MsgId::kTimerNavUpdate );
        smp.registerMessage<NavUpdateControlMsg>( MsgId::kNavUpdateControl );
        smp.registerMessage<DrivingStatusUpdateMsg>( MsgId::kDrivingStatusUpdate );
        // smp.registerMessage<EncoderUpdateMsg>( MsgId::kEncoderUpdate );
        smp.registerMessage<EncoderUpdateControlMsg>( MsgId::kEncoderUpdateControl );
        smp.registerMessage<BatteryLevelRequestMsg>( MsgId::kBatteryLevelRequest );
        // smp.registerMessage<BatteryLevelUpdateMsg>( MsgId::kBatteryLevelUpdate );
        // smp.registerMessage<ErrorReportMsg>( MsgId::kErrorReportFromPico );
        smp.registerMessage<TestPicoErrorRptMsg>( MsgId::kTestPicoReportError );
        smp.registerMessage<TestPicoMessagesMsg>( MsgId::kTestPicoMessages );
        // smp.registerMessage<PicoReceivedTestMsg>( MsgId::kPicoReceivedTestMsg );
        smp.registerMessage<DebugLinkMsg>( MsgId::kDebugSerialLink );
    }

    void setupEventProcessor( EventProcessor& ep )
    {
        ep.registerHandler<NullEventHandler>( EvtId::kNullEvent );

        ep.registerHandler<QuarterSecondTimerHandler>( EvtId::kQuarterSecondTimerEvent );
        ep.registerHandler<OneSecondTimerHandler>( EvtId::kOneSecondTimerEvent );
        ep.registerHandler<EightSecondTimerHandler>( EvtId::kEightSecondTimerEvent );

        ep.registerHandler<NavUpdateHandler>( EvtId::kNavUpdateEvent );
        ep.registerHandler<InitializeBNO055Handler>( EvtId::kBNO055InitializeEvent );
        ep.registerHandler<BNO055ResetHandler>( EvtId::kBNO055ResetEvent );
        ep.registerHandler<BeginCalibrationHandler>( EvtId::kBNO055BeginCalibrationEvent );
        ep.registerHandler<SendCalibrationInfoHandler>( EvtId::kSendCalibrationInfoEvent );

        ep.registerHandler<PulsePicoLedHandler>( EvtId::kPulsePicoLedEvent );

        ep.registerHandler<PicoResetHandler>( EvtId::kPicoResetEvent );

        ep.registerHandler<ErrorEventHandler>( EvtId::kErrorEvent );
    }

    void sendReady( SerialLinkPico& link )
    {
        std::uint32_t timeTick{ Clock::millis() };
        PicoReadyMsg ready( timeTick );
        ready.sendOut( link );

        output2cout( "CARRT Pico is ready" );
    }

}    // namespace

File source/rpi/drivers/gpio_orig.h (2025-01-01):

#ifndef PIGPIO_H
#define PIGPIO_H

#include <stddef.h>
#include <stdint.h>
#include <pthread.h>

#define PIGPIO_VERSION 79



#define PI_INPFIFO "/dev/pigpio"
#define PI_OUTFIFO "/dev/pigout"
#define PI_ERRFIFO "/dev/pigerr"

#define PI_ENVPORT "PIGPIO_PORT"
#define PI_ENVADDR "PIGPIO_ADDR"

#define PI_LOCKFILE "/var/run/pigpio.pid"

#define PI_I2C_COMBINED "/sys/module/i2c_bcm2708/parameters/combined"

#ifdef __cplusplus
extern "C" {
#endif

typedef struct
{
   uint16_t func;
   uint16_t size;
} gpioHeader_t;

typedef struct
{
   size_t size;
   void *ptr;
   uint32_t data;
} gpioExtent_t;

typedef struct
{
   uint32_t tick;
   uint32_t level;
} gpioSample_t;

typedef struct
{
   uint16_t seqno;
   uint16_t flags;
   uint32_t tick;
   uint32_t level;
} gpioReport_t;

typedef struct
{
   uint32_t gpioOn;
   uint32_t gpioOff;
   uint32_t usDelay;
} gpioPulse_t;

#define WAVE_FLAG_READ  1
#define WAVE_FLAG_TICK  2

typedef struct
{
   uint32_t gpioOn;
   uint32_t gpioOff;
   uint32_t usDelay;
   uint32_t flags;
} rawWave_t;


typedef struct
{
   uint16_t botCB;
   uint16_t topCB;
   uint16_t botOOL;
   uint16_t topOOL;
   uint16_t deleted;
   uint16_t numCB;
   uint16_t numBOOL;
   uint16_t numTOOL;
} rawWaveInfo_t;

typedef struct
{
   int clk;
   int mosi;
   int miso;
   int ss_pol;
   int ss_us;
   int clk_pol;
   int clk_pha;
   int clk_us;
} rawSPI_t;

typedef struct {
   uint32_t info;
   uint32_t src;
   uint32_t dst;
   uint32_t length;
   uint32_t stride;
   uint32_t next;
   uint32_t pad[2];
} rawCbs_t;

typedef struct
{
   uint16_t addr;
   uint16_t flags;
   uint16_t len;
   uint8_t  *buf;
} pi_i2c_msg_t;


#define BSC_FIFO_SIZE 512

typedef struct
{
   uint32_t control;
   int rxCnt;
   char rxBuf[BSC_FIFO_SIZE];
   int txCnt;
   char txBuf[BSC_FIFO_SIZE];
} bsc_xfer_t;


typedef void (*gpioAlertFunc_t)    (int      gpio,
                                    int      level,
                                    uint32_t tick);

typedef void (*gpioAlertFuncEx_t)  (int      gpio,
                                    int      level,
                                    uint32_t tick,
                                    void    *userdata);

typedef void (*eventFunc_t)        (int      event,
                                    uint32_t tick);

typedef void (*eventFuncEx_t)      (int      event,
                                    uint32_t tick,
                                    void    *userdata);

typedef void (*gpioISRFunc_t)      (int      gpio,
                                    int      level,
                                    uint32_t tick);

typedef void (*gpioISRFuncEx_t)    (int      gpio,
                                    int      level,
                                    uint32_t tick,
                                    void    *userdata);

typedef void (*gpioTimerFunc_t)    (void);

typedef void (*gpioTimerFuncEx_t)  (void *userdata);

typedef void (*gpioSignalFunc_t)   (int signum);

typedef void (*gpioSignalFuncEx_t) (int    signum,
                                    void  *userdata);

typedef void (*gpioGetSamplesFunc_t)   (const gpioSample_t *samples,
                                        int                 numSamples);

typedef void (*gpioGetSamplesFuncEx_t) (const gpioSample_t *samples,
                                        int                 numSamples,
                                        void               *userdata);

typedef void *(gpioThreadFunc_t) (void *);



#define PI_MIN_GPIO       0
#define PI_MAX_GPIO      53


#define PI_MAX_USER_GPIO 31


#define PI_OFF   0
#define PI_ON    1

#define PI_CLEAR 0
#define PI_SET   1

#define PI_LOW   0
#define PI_HIGH  1


#define PI_TIMEOUT 2


#define PI_INPUT  0
#define PI_OUTPUT 1
#define PI_ALT0   4
#define PI_ALT1   5
#define PI_ALT2   6
#define PI_ALT3   7
#define PI_ALT4   3
#define PI_ALT5   2


#define PI_PUD_OFF  0
#define PI_PUD_DOWN 1
#define PI_PUD_UP   2


#define PI_DEFAULT_DUTYCYCLE_RANGE   255


#define PI_MIN_DUTYCYCLE_RANGE        25
#define PI_MAX_DUTYCYCLE_RANGE     40000


#define PI_SERVO_OFF 0
#define PI_MIN_SERVO_PULSEWIDTH 500
#define PI_MAX_SERVO_PULSEWIDTH 2500


#define PI_HW_PWM_MIN_FREQ 1
#define PI_HW_PWM_MAX_FREQ      125000000
#define PI_HW_PWM_MAX_FREQ_2711 187500000
#define PI_HW_PWM_RANGE 1000000


#define PI_HW_CLK_MIN_FREQ       4689
#define PI_HW_CLK_MIN_FREQ_2711 13184
#define PI_HW_CLK_MAX_FREQ      250000000
#define PI_HW_CLK_MAX_FREQ_2711 375000000

#define PI_NOTIFY_SLOTS  32

#define PI_NTFY_FLAGS_EVENT    (1 <<7)
#define PI_NTFY_FLAGS_ALIVE    (1 <<6)
#define PI_NTFY_FLAGS_WDOG     (1 <<5)
#define PI_NTFY_FLAGS_BIT(x) (((x)<<0)&31)

#define PI_WAVE_BLOCKS     4
#define PI_WAVE_MAX_PULSES (PI_WAVE_BLOCKS * 3000)
#define PI_WAVE_MAX_CHARS  (PI_WAVE_BLOCKS *  300)

#define PI_BB_I2C_MIN_BAUD     50
#define PI_BB_I2C_MAX_BAUD 500000

#define PI_BB_SPI_MIN_BAUD     50
#define PI_BB_SPI_MAX_BAUD 250000

#define PI_BB_SER_MIN_BAUD     50
#define PI_BB_SER_MAX_BAUD 250000
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

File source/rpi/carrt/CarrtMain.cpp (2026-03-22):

#include <iostream>

#include "CarrtPigpio.h"
#include "DebugUtils.hpp"
#include "OutputUtils.hpp"



#if 0   // Use this to test that compile definitions inherit properly in cmake build

#if defined( USE_CARRTRPI0_STDIO ) && DEBUGUTILS_ON
    #pragma message "DEBUGUTILS_ON = ON"
#elif defined( USE_CARRTRPI0_STDIO )
    #pragma message "DEBUGUTILS_ON = OFF"
#else
    #pragma message "DEBUGUTILS_ON = undef"
#endif

#if defined( USE_CARRTRPI0_STDIO ) && USE_CARRTRPI0_STDIO
    #pragma message "USE_CARRTRPI0_STDIO = ON"
#elif defined( USE_CARRTRPI0_STDIO )
    #pragma message "USE_CARRTRPI0_STDIO = OFF"
#else
    #pragma message "USE_CARRTRPI0_STDIO = undef"
#endif

#if defined( DEBUGRPI0 ) && DEBUGRPI0
    #pragma message "DEBUGRPI0 = ON"
#elif defined( DEBUGRPI0 ) 
    #pragma message "DEBUGRPI0 = OFF"
#else
    #pragma message "DEBUGRPI0 = undef"
#endif

#if defined( BUILDING_FOR_RPI0 ) && BUILDING_FOR_RPI0
    #pragma message "BUILDING_FOR_RPI0 = ON"
#elif defined( BUILDING_FOR_RPI0 ) 
    #pragma message "BUILDING_FOR_RPI0 = OFF"
#else
    #pragma message "BUILDING_FOR_RPI0 = undef"
#endif

#if defined( USE_PIGPIOD ) && USE_PIGPIOD
    #pragma message "USE_PIGPIOD = ON"
#elif defined( USE_PIGPIOD ) 
    #pragma message "USE_PIGPIOD = OFF"
#else
    #pragma message "USE_PIGPIOD = undef"
#endif

#endif  // Checking compile definitions



int main(int, char**)
{
    gpioInitialise();

    std::cout << "Hello, from CarrtRpi!\n";

    debugM( "This is a debug message" );

    output2cout( "This is a conditional stdio message" );

    gpioTerminate();
}

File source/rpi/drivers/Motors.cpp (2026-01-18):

/*
    Motors.cpp - Functions for controlling CARRTv3's drive motors

    Copyright (c) 2026 Igor Mikolic-Torreira.  All right reserved.

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
    You should have received a copy of the GNU General Public License
    along with this program.  If not, see <http://www.gnu.org/licenses/>.
*/

#include "Motors.h"

#include <cstdint>

#include "I2c.h"
#include "PCA9685.h"

// Extend namespace with additional functions and such
namespace Motors
{

    enum
    {
        kRightRearMotorNbr = 0,
        kRightFrontMotorNbr = 1,
        kLeftFrontMotorNbr = 2,
        kLeftRearMotorNbr = 3
    };

    const int kNbrMotors = 4;

    const std::uint8_t kMotorHatAddress = 0x60;

    class Motor
    {
    public:
        Motor( int pwmPin, int pinA, int pinB );
        ~Motor();

        void goForward() { motorCommand( Motors::kCmdForward ); }

        void goBackward() { motorCommand( Motors::kCmdBackward ); }

        void stop() { motorCommand( Motors::kCmdRelease ); }

        void motorCommand( Motors::MotorCmd cmd );
        void setSpeed( int speed );

    private:
        std::uint8_t mPwmPin;
        std::uint8_t mPinA;
        std::uint8_t mPinB;
    };

    void motorCommand( std::uint8_t motorA, std::uint8_t motorB,
                       std::uint8_t cmd );

    Motor* mMotors[ kNbrMotors ];

};    // namespace Motors

Motors::Motor::Motor( int pwmPin, int pinA, int pinB )
    : mPwmPin( static_cast<std::uint8_t>( pwmPin ) ),
      mPinA( static_cast<std::uint8_t>( pinA ) ),
      mPinB( static_cast<std::uint8_t>( pinB ) )
{
    // Nothing else to do
}

Motors::Motor::~Motor() { stop(); }

[[maybe_unused]]
void Motors::Motor::motorCommand( Motors::MotorCmd cmd )
{
    switch ( cmd )
    {
        case Motors::kCmdForward:
            // Set pin A = 1;
            // Set pin B = 0;
            PCA9685::setOn( kMotorHatAddress, mPinA );
            PCA9685::setOff( kMotorHatAddress, mPinB );
            break;

        case Motors::kCmdBackward:
            // Set pinA = 0;
            // Set pinB = 1;
            PCA9685::setOff( kMotorHatAddress, mPinA );
            PCA9685::setOn( kMotorHatAddress, mPinB );
            break;

        case Motors::kCmdRelease:
        case Motors::kCmdBrake:
            // Set PinA = 0;
            // Set PinB = 0;
            PCA9685::setOff( kMotorHatAddress, mPinA );
            PCA9685::setOff( kMotorHatAddress, mPinB );
            break;
    }
}

void Motors::Motor::setSpeed( int speed )
{
    PCA9685::setPwm( kMotorHatAddress, mPwmPin, 0,
                     static_cast<std::uint16_t>( speed * 16 ) );
}

void Motors::init()
{
    PCA9685::init( kMotorHatAddress );

    mMotors[ 0 ] = new Motor( 8, 9, 10 );
    mMotors[ 1 ] = new Motor( 13, 12, 11 );
    mMotors[ 2 ] = new Motor( 2, 3, 4 );
    mMotors[ 3 ] = new Motor( 7, 6, 5 );

    setSpeedAllMotors( Motors::kFullSpeed );
}

void Motors::setSpeedAllMotors( int speed )
{
    for ( int i = 0; i < kNbrMotors; ++i )
    {
        mMotors[ i ]->setSpeed( speed );
    }
}

void Motors::goForward()
{
    for ( int i = 0; i < kNbrMotors; ++i )
    {
        mMotors[ i ]->goForward();
    }
}

void Motors::goBackward()
{
    for ( int i = 0; i < kNbrMotors; ++i )
    {
        mMotors[ i ]->goBackward();
    }
}

void Motors::stop()
{
    for ( int i = 0; i < kNbrMotors; ++i )
    {
        mMotors[ i ]->stop();
    }
}

void Motors::rotateLeft()
{
    // Right side goes forward
    mMotors[ Motors::kRightFrontMotorNbr ]->goForward();
    mMotors[ Motors::kRightRearMotorNbr ]->goForward();

    // Left side goes backward
    mMotors[ Motors::kLeftFrontMotorNbr ]->goBackward();
    mMotors[ Motors::kLeftRearMotorNbr ]->goBackward();
}

void Motors::rotateRight()
{
    // Right side goes backward
    mMotors[ Motors::kRightFrontMotorNbr ]->goBackward();
    mMotors[ Motors::kRightRearMotorNbr ]->goBackward();

    // Left side goes forward
    mMotors[ Motors::kLeftFrontMotorNbr ]->goForward();
    mMotors[ Motors::kLeftRearMotorNbr ]->goForward();
}

[[maybe_unused]]
void Motors::setRearRightMotorSpeed( int s )
{
    mMotors[ Motors::kRightRearMotorNbr ]->setSpeed( s );
}

[[maybe_unused]]
void Motors::setFrontRightMotorSpeed( int s )
{
    mMotors[ Motors::kRightFrontMotorNbr ]->setSpeed( s );
}

[[maybe_unused]]
void Motors::setFrontLeftMotorSpeed( int s )
{
    mMotors[ Motors::kLeftFrontMotorNbr ]->setSpeed( s );
}

[[maybe_unused]]
void Motors::setRearLeftMotorSpeed( int s )
{
    mMotors[ Motors::kLeftRearMotorNbr ]->setSpeed( s );
}

[[maybe_unused]]
void Motors::runRearRightMotor( Motors::MotorCmd cmd )
{
    mMotors[ Motors::kRightRearMotorNbr ]->motorCommand( cmd );
}

[[maybe_unused]]
void Motors::runFrontRightMotor( Motors::MotorCmd cmd )
{
    mMotors[ Motors::kRightFrontMotorNbr ]->motorCommand( cmd );
}

[[maybe_unused]]
void Motors::runFrontLeftMotor( Motors::MotorCmd cmd )
{
    mMotors[ Motors::kLeftFrontMotorNbr ]->motorCommand( cmd );
}

[[maybe_unused]]
void Motors::runRearLeftMotor( Motors::MotorCmd cmd )
{
    mMotors[ Motors::kLeftRearMotorNbr ]->motorCommand( cmd );
}

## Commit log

2017-11-11 Initial versions of most fundamental drivers
2017-11-11 Standardized the error reporting in the i2c driver
    [I2c.cpp]
2017-11-12 Correct return values to be -1 for error, 0 for no error
    [I2c.cpp]
2017-11-12 Add print() functions to the LCD capabilities (using templates)
2017-11-12 Implement millis() and micros() functions
2017-11-12 Cut down the number of test loops
2017-11-19 Restore error reporting via cerr
    [I2c.cpp]
2017-11-19 Add driver for PCA9685 PWM board
2017-11-19 Correct compiler errors for PCA9685 driver
    [PCA9685.cpp]
2017-11-19 Correct typo in function name
    [PCA9685.cpp]
2017-11-30 Add a setPin() function to PCA9685 driver
2017-11-30 Initial commit of motor drivers
2017-11-30 Complete funtion implementation and fix up return types
    [Motors.cpp]
2019-06-02 Shift error handling to be exception-based
    [I2c.cpp, Lcd.cpp, PCA9685.cpp]
2019-06-02 Add photo of CARRT3 prototype for testing electronics
2019-06-05 Add try-catch blocks to test drivers.
2019-06-09 Added Driver code (and tests) for the motors that power the wheels
2019-06-09 Minor tweaks to test drivers for keypad and lcd
2019-06-09 Adjust timings on collective motor test to allow current measurements
2019-06-09 Update with transistor and resistor calculation results
2019-06-10 Convert i2c to use pigpio library
2019-06-11 Fix with correct pigpio function call for i2c block data transfer
    [I2c.cpp]
2019-06-11 Implement error code scheme that uniquely identifies modules and functions
    [I2c.cpp]
2019-08-24 Photo showing prototype board with motors connected (and working)
2023-11-19 Initial checkin, switch from AVR to PICO
2023-11-23 Fixes (primary: us to ms; big oops!)
    [CarrtPicoMain.cpp]
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2023-12-02 Be more careful with I2C in KeypadTest
2023-12-03 Update with poweroff button config info
2023-12-08 Update to use new error ID creation function
    [I2c.cpp]
2023-12-10 Update info for 6 battery motor configuration
2023-12-10 Update wiring color scheme
2023-12-10 Add PowerBoost and BNO055 connections
2024-06-08 Fix I2C error throws
    [I2c.cpp]
2024-06-09 Add notes on wiring Pico debugger
2024-06-19 Add binary info to pico builds
2024-06-23 Start fleshing out cmds between Pi-0 and Pico
2024-06-27 Make a shared error code scheme
    [I2c.cpp]
2024-06-28 Test exception handling in Pico build
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2024-07-06 Add a check on how long the interrupt takes
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2024-07-06 Fix names of #defines to avoid clashes with SDK
    [CarrtPicoBinaryInfo.cpp, CarrtPicoDefines.h, CarrtPicoMain.cpp]
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2024-07-07 Use heartbeat LED to signal trouble with a fast pulse
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2024-07-08 Test Pico reset/reboot.
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2024-07-23 Added function to submodule to get all calibration statuses at once
2024-07-25 Revise start-up process because of the way BNO055 calibration works
2024-07-26 Mark that we need to fix error handling here
    [Core1.cpp]
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2024-12-27 Add schematics
    [CARRTv3.kicad_pcb, CARRTv3.kicad_sch]
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2024-12-27 Added level-shifters, LIDAR, etc
    [CARRTv3.kicad_sch]
2024-12-28 Updated to use voltage shifters
    [CARRTv3.kicad_sch]
2024-12-28 Update gitignore to omit PDFs except the schematic PDF
2024-12-28 Color-coded the wiring
    [CARRTv3.kicad_sch]
2024-12-29 Cleaned up wiring, added labels
    [CARRTv3.kicad_sch]
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2024-12-31 Add buzzer, missing OE & GND wires, clean up wiring
    [CARRTv3.kicad_sch]
2025-01-01 add cmake infrastructure for switching pigpio <-> pigpiod
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2025-01-04 Fix erroneous type cast
    [I2c.cpp]
2025-01-04 Update to exact pins being used; update colors of wires to actual; cosmetic repositionings
    [CARRTv3.kicad_sch]
2025-03-02 Updated schematics to reflect implementation wiring adjustments
    [CARRTv3.kicad_sch]
2025-04-06 Correct current values
2025-04-06 Reflect actual wiring of BSS138
    [CARRTv3.kicad_sch]
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2025-04-09 Initial fully wired assembly (missing Lidar)
2025-07-02 Make RPi0 pin assignments explicit in one header
2025-07-02 Add buzzer driver and test
    [Buzzer.cpp]
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2025-07-20 Initial checkin of Lidar code from old-carrt (needs conversion)
2025-07-22 Initial conversion of Lidar (with some new I2C functions too)
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2025-07-25 Update schematics for UBEC, etc
    [CARRTv3.kicad_sch]
2025-07-26 Switch ADC0-ADC1 connections; update schematic and connections tables
    [CARRTv3.kicad_sch]
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2025-08-03 Create Serial link implementation for Pico (and fix little serial things in the process)
    [I2C.cpp, SerialLinkPico.cpp]
2025-08-04 Back to block reading over uart. Now working.
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2025-08-09 Switch to using references, not pointers in CriticalSection
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2025-08-23 Update connections notes to include Pico SWD connects
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2025-08-30 Fix typo in Encoders.cpp
    [Encoders.cpp]
2025-08-30 Fix error in 1/4s events, clean up code a bit
    [Core1.cpp]
2025-08-30 Small fixes to BNO055 code and CMakeLists.txt files
    [BNO055.cpp]
2025-08-30 Manage state info in Pico with singleton (can accomodate atomic if needed)
2025-08-31 Added more cmds, including reset (pico) and implementation for this. Ordered commands in code by orderof Cmd IDs in SerialCommand.h
    [CarrtPicoMain.cpp]
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2025-09-05 Make I2C functions used by BNO055.c library code extern "C"
2025-09-21 Correct I2C connects at Pico
    [CARRTv3.kicad_sch]
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2025-09-27 Fix I2C implementation for comms with BNO055
    [I2C.cpp]
2025-10-06 Fix loading of calib status struct
    [BNO055.cpp]
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2025-10-06 Implement calibration cmds and fix some bugs
2025-10-11 Clean up events and code related to nav calibration
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2025-10-11 Add BNO reset event
    [Core1.cpp]
2025-10-11 Improve BNO055 init and reset to avoid event queue overflows
    [BNO055.cpp]
2025-10-12 Incorporate lessons from BNOTest into Carrt Pico itself
2025-10-13 Set reserve size for classes with unordered_maps; fix missing includes
    [CarrtPicoMain.cpp]
2025-10-13 Add msg to control msg sending from Pico
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2025-10-20 Implement message to test error reporting. Also make sure never dual "takeAction()"
    [CarrtPicoMain.cpp]
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2025-10-26 Fix handling of calibration begin and add new autoCalibration mode/state.
    [Core1.cpp]
2025-10-27 Track whether we are in startup mode (some calibration reporting and calibration itself needs to be off during startup)
2025-10-29 Configyre encoders to interrupt on Core1 (not Core0)
2025-11-02 Made OutputUtils adapted to both RPi0 and Pico
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2025-11-15 Switch to target_sources in CMakeLists and also omit compile defs and options inherited from libs in cmake build
2025-11-15 Add optional code to check correct inherit of compile opts and defs
    [CarrtMain.cpp]
2025-11-15 Improve code for checking compile opts/defs inherited from libs correctly
    [CarrtPicoMain.cpp]
2025-11-18 Add ability to control individual timer events (not all or nothing)
2025-11-18 Ensure path for "pico.h" in included in config (needed to include "OutputUtils.h")
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2025-11-27 This is the serial FIX (Pico needs small pause for serial traffic to arrive in sequential element reads)
2025-11-27 Roll-back debugging code (problem fixed)
    [CarrtPicoMain.cpp]
2025-11-27 Rename ResetMsg to ResetPicoMsg for clarity
    [CarrtPicoMain.cpp]
2025-11-27 Pico also sends ResetPicoMsg (to inform RPi it is resetting
2025-11-28 Refine Pico delays (and min delay for sequential serial reads)
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2025-11-28 Update how timer and nav msgs are turned on/off via msgs from RPi)=0
2025-12-28 For testing, add ack of msg requested by RPi0 but that Pico doesn't actually ever send.
2025-12-29 Control Pico in detail debug of Serial Msgs using build system passed #define
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2026-01-02 Change ErrorReportMsg to include a time hack
    [CarrtPicoMain.cpp]
2026-01-02 Allow a few more attempts when reading data on Pico
2026-01-04 Clean up missing std:: prefix on uint_xx
    [SerialLinkPico.cpp]
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2026-01-04 Implement Pico get4Bytes() to make multiple read attempts
2026-01-06 This combo of small pause and attempts seems to work well for Pico
2026-01-06 Need to up pico read attempts to 16
2026-01-07 Fix usage of cmake config:debug.
    [CarrtMain.cpp]
2026-01-07 Fix #ifdef that should be #if
    [CarrtPicoDefines.h]
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2026-02-16 Have 8s timer events toggle the singal pin on and off
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2026-02-16 Update serial msgs for Encoders to pass side, count
2026-02-16 Update to reflect new encoder update msg format
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2026-02-17 Incorporate battery voltage checking into events and handlers
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2026-02-18 Add simple Serial Rcvr that dumps all messages received from Pico.
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2026-03-01 Clean up generation of header with current git HEAD hash
2026-03-01 Fix depending on current branch and the heads of each
2026-03-01 Fix cmake implementation of build info for Pico
2026-03-01 Minimal initial implementation of build info within Pico executable
2026-03-03 Correct handling of battery msgs and MsgControlMsg processing of battery msg settings
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2026-03-03 Incorporate new msgs and also silence Pico at start of test
2026-03-07 Correct the GPIO nbrs for the GPIOs connected to the encoders.
    [CarrtPicoDefines.h]
2026-03-07 Correct names of CARRTPICO_SERIAL_LINK_UART_?X_PIN from _PIN to _GPIO (reflects what they really are)
    [CarrtPicoBinaryInfo.cpp, CarrtPicoDefines.h, SerialLinkPico.cpp]
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2026-03-07 Correct GPIO pin labels
    [CarrtPicoBinaryInfo.cpp]
2026-03-09 Rename FailtSafe -> NoFail
    [CarrtPicoMain.cpp]

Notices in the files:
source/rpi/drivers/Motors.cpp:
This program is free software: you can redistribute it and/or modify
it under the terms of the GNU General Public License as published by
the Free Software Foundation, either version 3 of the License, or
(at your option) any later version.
